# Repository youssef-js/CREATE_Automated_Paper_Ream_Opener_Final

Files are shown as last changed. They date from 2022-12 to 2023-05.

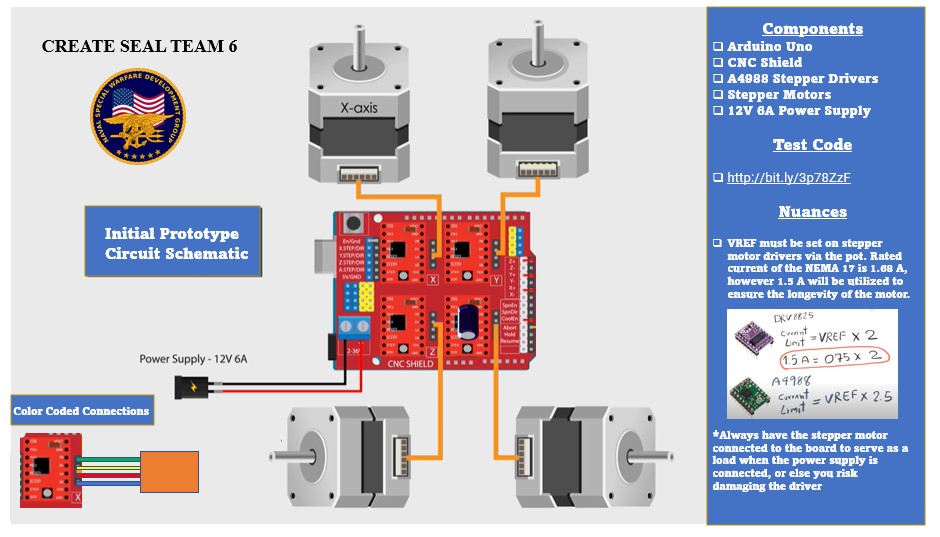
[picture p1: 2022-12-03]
Misc/CREATE_Circuit_Schematic.jpg

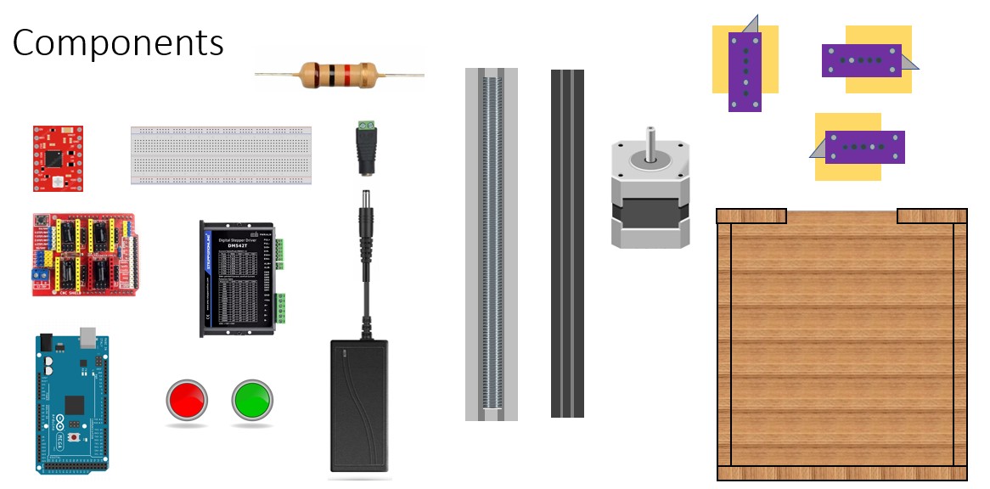
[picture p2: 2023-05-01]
Misc/CREATE_Final_Components.jpg

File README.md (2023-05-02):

# CREATE-Competition-Automated-Paper-Ream-Opener

 Fall 2022 - Spring 2023 
 ECE Design Lab
 
 The Center for Disability Services mailing center, which processes enormous amounts of mail per day
supporting official New York State mailing operations, has partnered with students to develop a system that assists
disabled workers. The center uses an estimated 50,000 – 100,000 pieces of paper per day. This paper is manually
opened from reams of paper containing 500 sheets each, therefore, approximately 100-200 reams of paper must be
opened per day. The center would like to hire people with disabilities to open the reams of paper, but this is difficult due
to physical dexterity issues and the large number of paper cuts the disabled workers often suffer when trying to do this
job. 

The goal of this project is to develop a system that automatically opens reams of paper in a safe and effective way.

 ### Repository Contents
 
 In the interest of transparency all project reports have been included. Reading through this documentation will provide an individual with information on key milestones that were achieved during the progressive evolution of the product. Specifically the "Reports" folder contains the following: 
 
 * Logical Design Report
 * Physical Design Report
 * Experimental Design Report 
 * CREATE_Experimental_Results_and_Discussion

 Furthermore, within the "Presentations" folder viewers have been provided with a final copy of the presentation slides for both the fall and spring semesters utilized within the classroom setting that exemplify the accomplished work within a condensed format.

 Lastly, in the scenario where an individual may wish to replicate the design we have provided the source code from the Fall and Spring semester that is used to control the logic behind the device. The initial circuit schematic, initial preliminary prototype model, final circuit schematic, final 3D model and lastly a compilation of the fianl components being used have also been included, these can be found within the "Misc" folder.
 
  ### System Parts
  
  The system was designed with the intention of being completely reproducible by any individual with the desire to do so. As such for the convenience of the prospective designer, the utilized components and their respective links are compiled below:
  
  1. Drive System Components

     * Belt Driven Nema 17: 500mm 1070-Bundle
  
       Link: https://openbuildspartstore.com/v-slot-nema-17-linear-actuator-bundle-belt-driven/
       
     * Belt Driven Nema 17: 500mm 1070-Bundle
  
       Link: https://openbuildspartstore.com/v-slot-nema-17-linear-actuator-bundle-belt-driven/
       
     * Belt Driven Nema 17: 250mm 1070-Bundle
  
       Link: https://openbuildspartstore.com/v-slot-nema-17-linear-actuator-bundle-belt-driven/
       
     * STEPPERONLINE NEMA 23 Stepper Motor 3.0A
  
       Link: https://www.amazon.com/gp/product/B077Z5QJCL/ref=ewc_pr_img_2?smid=AWQBCGWISS7BL&psc=1
       
     * NEMA23 Stepper Motor Mounting Plate
  
       Link: https://www.amazon.com/gp/product/B0836P59M4/ref=ppx_yo_dt_b_search_asin_title?ie=UTF8&psc=1
       
     * Saiper 5pcs GT2 20 Teeth 6.35mm Bore Timing Pulley
  
       Link: https://www.amazon.com/gp/product/B07MGMBX3N/ref=ewc_pr_img_3?smid=A3ILYKI8R26I7D&th=1
       
     * Threaded Rod with Cart and NEMA Stepper Motor Apparatus
  
       -Obtained from Public Laboratory Supplies, it had been fully assembled by another individual

  2. Control-Oriented Components
  
     * CNC Shield Expansion Board V3.0 + 4Pcs A4988 Stepper Motor Driver
  
       Link: https://www.amazon.com/Shield-Expansion-Stepper-Engraver-Printer/dp/B07DXNZ9PS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

     * 12V 6A Power Supply
  
       Link: https://www.amazon.com/Signcomplex-Supply-Transformer-Switching-Adapter/dp/B074HV582Q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

     * 24V 6A Power Supply
  
       Link: https://www.amazon.com/Adapter-100-240V-Transformers-Security-Computers/dp/B08Z7X9F1V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
       
     * Arduino Mega 
  
       Link: https://www.amazon.com/ELEGOO-ATmega2560-ATMEGA16U2-Projects-Compliant/dp/B01H4ZDYCE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
       
  3. Crucial Supplies
 
     * Wires
  
       Link: https://www.amazon.com/dp/B08B8XX89H/ref=twister_B09H6XQRJG?_encoding=UTF8&th=1
       
     * Bulk Pack of A4988 Stepper Motor Drivers
  
       Link: https://www.amazon.com/HiLetgo-Stepstick-Stepper-Printer-Compatible/dp/B07BND65C8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

     * DM542T STEPPERONLINE CNC Stepper Motor Driver
  
       Link: https://www.amazon.com/STEPPERONLINE-1-0-4-2A-20-50VDC-Micro-step-Resolutions/dp/B06Y5VPSFN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
       
     * DM542T STEPPERONLINE CNC Stepper Motor Driver
  
       Link: https://www.amazon.com/STEPPERONLINE-1-0-4-2A-20-50VDC-Micro-step-Resolutions/dp/B06Y5VPSFN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
       
     * 18mm Snap-off Blades by HEIKIO
  
       Link: https://www.amazon.com/Snap-Off-50-Pack-Quality-Stainless-Replacement/dp/B07XRTWWMS
       
     * LED Illuminated Push Buttons
  
       Link: https://www.amazon.com/gp/product/B01M7PNCO9/ref=ox_sc_act_title_1?smid=A3H7VB6FZ4M9FM&psc=1
       
     * 2pcs 2040 V Slot 600mm Aluminum Extrusion
  
       Link: https://www.amazon.com/dp/B0B9WY6PK9?ref=ppx_yo2ov_dt_b_product_details&th=1
       
     * 460PCS M4 Screws Metric Button Head
  
       Link: https://www.amazon.com/gp/product/B09YM7V1JC/ref=ppx_yo_dt_b_asin_title_o02_s00?ie=UTF8&th=1
       
     * Iverntech 20pcs Black Aluminum Corner Bracket
  
       Link: https://www.amazon.com/dp/B091GH5QKF?ref=ppx_pop_mob_ap_share&th=1

  4. Store-Bought Components
  
     * Wooden Planks
  
       Store: Home Depot
     
     * Acrylic Top Cover
  
       Store: Lowes

 ### Itemized Expenses
  
| Category | Item | Price |
| --- |:---:| -----:|
| Drive System |Belt Driven Nema 17: 500mm 1070-Bundle |$117.99|
| |Belt Driven Nema 17: 500mm 1070-Bundle |$117.99|
| |Belt Driven Nema 17: 250mm 1070-Bundle |$111.99|
| |STEPPERONLINE NEMA 23 Stepper Motor 3.0A |$31.98 |
| |NEMA23 Stepper Motor Mounting Plate |$9.49  |
| |Saiper 5pcs GT2 20 Teeth 6.35mm Bore Timing Pulley |$8.39  |
| |Threaded Rod with Cart and NEMA Stepper Motor Apparatus |FREE |
| | | |
| Control-Oriented Components|CNC Shield Expansion Board V3.0 + 4Pcs A4988 Stepper Motor Driver  |$15.39 |
| |12V 6A Power Supply |$19.99 |
| |24V 6A Power Supply |$15.98 |
| |Arduino Mega |$20.99 |
| | | |
| Crucial Supplies | Wires |$14.94 |
| |Bulk Pack of A4988 Stepper Motor Drivers |$9.89  |
| |DM542T STEPPERONLINE CNC Stepper Motor Driver |$28.99 |
| |DM542T STEPPERONLINE CNC Stepper Motor Driver |$28.99 |
| |18mm Snap-off Blades by HEIKIO |$21.99 |
| |LED Illuminated Push Buttons |$18.86 |
| |2pcs 2040 V Slot 600mm Aluminum Extrusion |$86.97 |
| |460PCS M4 Screws Metric Button Head |$17.99 |
| |Iverntech 20pcs Black Aluminum Corner Bracket |$18.99 |
| | | |
|Store-Bought |Wooden Planks |Stakeholder Expense|
| |Acrylic Top Cover |Stakeholder Expense| 
| | | |
|Grand Total |-------------  |$717.79|

   ### Software Dependencies
   
   In the context of software dependencies there is none for the traditional user. This apparatus requires no external downloads and is advertised as a complete stand-alone product.
   
However, when initially setting up the device one must upload the source code onto the microcontroller. The first step is to download the Arduino IDE, the appropriate link is found below:

Link: https://www.arduino.cc/en/software

At this stage the setup in terms of software has been completed. Please download the source code provided within this repository and upload to the microcontroller to begin using the apparatus.

### Replication

In the interest of successfully replicating the aforementioned progress a concise check list has been provided below.

 1. Watch the instructional videos provided below:
  
     Basics
     * Link: https://www.screencast.com/t/LzzzPJ7e0wt

     Assembly of Linear Rail Kits
     * Link: https://www.youtube.com/watch?v=tHn-gffborc&ab_channel=OpenBuilds

     Specifics of Analog Blade Holders
     * Link: https://youtu.be/Tv00ml124e8

     NYSID CREATE Final Video Submission
     * Link: https://www.youtube.com/watch?v=cMDn14l95jw&ab_channel=MazinChater
       
Now that sufficient context has been provided an individual would proceed by purchasing the displayed equipment articulated within the video format. A complete list of parts with purchasing links has been organized up above in the "System Parts" section.
    
  2. Purchase Relevant Equipment
  
Lastly, the final step of the procedure is to recreate the circuit connections displayed within the "Misc" folder of this repository. After this has been accomplished an indvidual may upload the source code to the microcontroller.
    
  3. Follow Circuit Schematic and Upload Source Code
 
It will be known whether or not successful replication has been achieved based on the performance of the apparatus in comparison to the ideal case displayed in the instructional video.

### NYSID CREATE Competition



1st place finish at the NYSID CREATE competition. 
Beyond the prize money, the work is having a real impact.  It has enabled the Center for Disability Services Mailing Center to hire additional workers with disabilities.
### Personnel and Funding

This project is completely sponsored by New York State Industries for the Disabled (NYSID) and allows the respective designers to take part in the CREATE (Cultivating Resources for Employment with Assistive TEchnology) competition.

Designers

1. Youssef Jalwaj Soubai

2. Mazin Chater

3. Abdullah Qureshi

Faculty Mentors/Support

1. Jonathan Muckell

2. Mike Denmark

Special thanks to Alex Demitraszek, customer care manager of the Center for Disability Services.

Developed in ECE490: Design Lab; in the Electrical & Computer Engineering Department.

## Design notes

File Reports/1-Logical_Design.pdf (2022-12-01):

PP-2017 V2.1

ANALYSIS & LOGICAL DESIGN | 1

# CREATE Competition: Automated Ream Opener (Analysis & Logical Design)

Abdullah Qureshi, Youssef Jalwaj-Soubai, Mazin Chater

Activity Report

Abstract—The Center for Disability Services mailing center, which processes enormous amounts of mail per day supporting official New York State mailing operations, has partnered with students to develop a system that assists disabled workers. The center uses an estimated 50,000 – 100,000 pieces of paper per day. This paper is manually opened from reams of paper containing 500 sheets each, therefore, approximately 100-200 reams of paper must be opened per day. The center would like to hire people with disabilities to open the reams of paper, but this is difficult due to physical dexterity issues and the large number of paper cuts the disabled workers often suffer when trying to do this job. The goal of this project is to develop a system that automatically opens reams of paper in a safe and effective way.

Index Terms—Arduino, NEMA, automated ream opener

✦

### 1 THE PROBLEM

MAILING centers typically require large quantities of paper to meet their daily demands. As such, reams of paper must be opened safely and efficiently in a proportionally high demand. The Center for Disability Services would like to develop a system which meets these requirements particularly as a tool to assist disabled workers. A viable solution would decrease time to open each ream while simultaneously being safe and accessible to disabled workers. Ideally, it would also allow the Center for Disability Services to hire additional disabled individuals specifically to operate the final system.

### 2 INSPIRATION

When doing background research on the topic, there was no automated system that opened

- Mazin Chater ,
E-mail: mchater3@albany.edu
- Youssef Jalwaj-Soubai ,
E-mail: yjalwaj-soubai@albany.edu
- Abdullah Qureshi ,
E-mail: aqureshi@albany.edu
Electrical and Computer Engineering Department University at Albany

a ream of paper. There were implementations that operated on paper, however. Of these, most relevant was an automated letter opener and an Arduino based paper cutter. When considering the former, it was worth noting how the letters were opened precisely without damaging the inside contents. This is a similar amount of space between the outside sheet and interior paper of a ream, leading to the conclusion that a blade of high precision could open the outside sheet without cutting any interior papers. Of the latter, the Arduino based paper cutter used a NEMA stepper motor to move a blade left and right perpendicular through a sheet of paper, thereby making equal cuts of length specified by the user. This design led to an epiphany regarding the use of a stepper motor to cut across potentially each of the four sides of the ream to separate the outside layer.

### 3 DESIGN CONSTRAINTS

There are limitations placed on a potential implementation. Most evidently, testing will be a primary focus and is somewhat limited due to the lack of readily available access to reams of paper. Additionally, funds are limited and restrain the amount of trial-and-error in terms

Activity Report

2 | ANALYSIS & LOGICAL DESIGN

of system designing. Finally, there is a deadline
of completion by April 2023.
- Testing: Although available in high capacity at the Center for Disability Services mailing center, it is limiting to consider scheduling, travel, etc to perform frequent tests.
- Cost: The Center for Disability Services has allocated a balance of one thousand dollars to build the desired system.
- Time: The design should be complete and in use well before the start of the CREATE design competition in April.

### 4 PROPOSED SOLUTION

The proposed device is a preliminary prototype that reflects the designers aptitude towards testing. Focusing on this notion the following engineering diagram has been developed. An individual should take head that the inspiration from the letter opener is the driving concept for this implementation.

### 4.1 Engineering Diagram

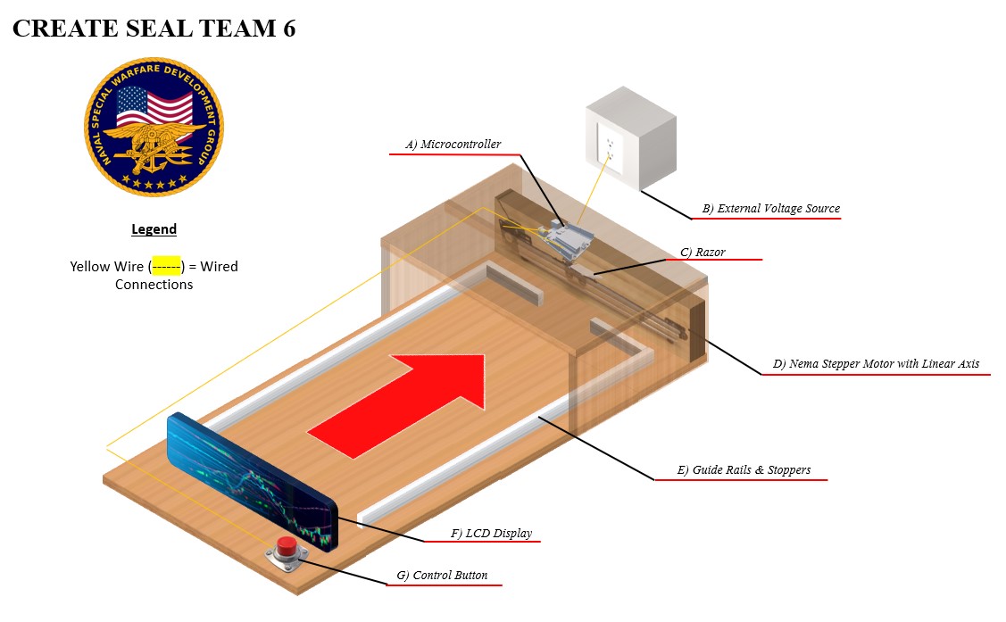
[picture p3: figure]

Figure 1. Annotated diagram of the proposed solution.

Physically speaking the device is quite simple in nature and requires minimal overhead to implement. The design is centered around a linear axis rail operated by a NEMA stepper motor. This contraption is capable of controlled uniform movement and as such when a razor blade is attached to the sliding linear cart it will ideally make clean lacerations to the paper ream cover. A user interacts with the system via a button press that controls the operation of the linear rail. Along the base of the apparatus there are guiding protuberances that orient the ream in the most optimal setting. These ”stoppers” ensure that only the cover of the ream will be slit, thereby leaving the contents unperturbed.

### 4.2 System Requirements

4.2.1 System User
The user that will interact with the system is an employee from the Center for Disability Services mailing center. All that will be asked of this individual is the ability to lift and push a ream of paper into its proper setting as well as the ability to push a button. If both of these qualities are satisfied one will have no issue operating the proposed solution.

4.2.2 Functional Requirements
Following are the most important functional requirements.
1) Paper Ream Cutting Ability: The system should have the ability to slit the desired ends of the paper ream in order to make the paper ream opening easy.
2) Safety: Since the users of the system are physically disabled, its a mandatory requirement of the system to be completely safe to use.
3) Ease of Use: Since the users of the system are physically disabled, its a mandatory requirement of the system to be very easy to use.

4.2.3 Non-Functional Requirements Following are the most important non-functional requirements of the system.
1) Capacity: The system should have the ability to open 200 reams of paper a day.
2) Ability to work with different ream size: It is a desired quality of the system to be able to work with different size of paper reams.
3) Complete Package Opening: Ideally the system should be able to completely open the paper ream although cutting the ends of the paper ream is sufficient.

PP-2017 V2.1

SURNAME et al. | 3

### 4.3 Justification

The belt driven actuator design was chosen
mainly because of its ease of use and paper ream opening ability. The current design is easier to use than the moving arm package opener because it is more compact and will potentially contain a single button to control the blade. The idea of a moving arm package opener design was built around two arms that go into the flaps of the paper ream and then move along the y axis to tear the paper ream. The moving arm package opener design was safer to use because it did not contain the a cutting blade but it would not be easy to use and would be very less compact. Based on these results our team decided to go with the belt driven actuator design.

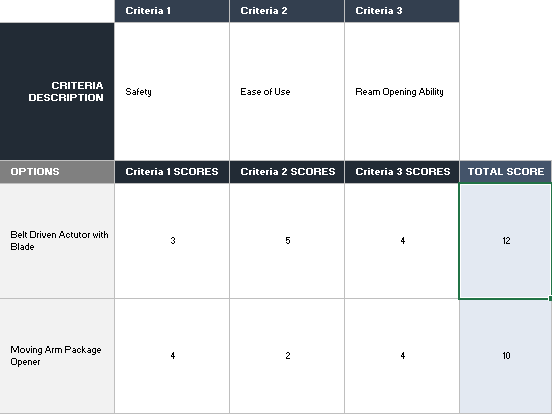
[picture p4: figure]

Figure 2. Decision Matrix

### 4.4 Ethical Concerns

One of the most important ethical concerns that our design addresses is user safety. Since our design contains a blade that moves along the x axis to open the ream of paper, the danger of a user getting a cut increases dramatically. In order to mitigate potential harm caused by the system the belt driven actuator with blade will be put into a wooden box such that the only thing that can be put in to the box is just the ream of paper. Moreover, the stepper motors that control the motion will be controlled by a button. This will ensure that the stepper motors does not cause the blade to move without user input.

### 5 INITIAL PROTOTYPE

Our initial prototype consists of a wooden box with a belt driven actuator to which a blade is attached. The belt driven actuator allows the blade to move along the x axis. The belt driven actuator is controlled by a stepper motor, which allows movement in the positive and negative x axis. In order to ensure the safety of the user, the control of the stepper motor will be done by a button outside the wooden casing. The user will place the paper ream inside the apparatus, the stoppers will restrict the user from pushing the paper ream too close to the blade. After placing the paper ream , the user will push the button for the actuator to start and the blades will make a cut to the specific side of the paper ream. The user can switch the side of the paper ream to apply cuts on different sides of the paper ream to make the package easier to open. After applying the cuts the user can take the paper ream and dump the contents. One prospective engineering problem that might cause delays is finding the optimal distance for which to stop the paper ream, such that the blade does not cause damage to the paper inside the ream. One solution to the problem is experimenting with the reams and through trial and error finding the specific distance that will allow for the package to be cut without harming the paper inside.

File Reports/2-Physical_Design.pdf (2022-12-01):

PP-2017 V2.1

PHYSICAL DESIGN | 1

# Automated Ream Opener

# (Physical Design)

Mazin Chater, Abdullah Qureshi, Youssef Jalwaj-Soubai

Activity Report

✦

### 1 PHYSICAL DESIGN

### 1.1 Engineering Diagram


Figure 1. Annotated diagram of the proposed solution.

Physically speaking the device is quite simple in nature and requires minimal overhead to implement. The design is centered around a linear axis rail operated by a NEMA stepper motor. This contraption is capable of controlled uniform movement and as such when a razor blade is attached to the sliding linear cart it will ideally make clean lacerations to the paper ream cover. A user interacts with the system via a button press that controls the operation

- Mazin Chater,
E-mail: mchater3@albany.edu,
- Youssef Jalwaj-Soubai,
E-mail: yjalwaj-soubai@albany.edu,
- Abdullah Qureshi,
E-mail: aqureshi@albany.edu, University at Albany.

of the linear rail. Along the base of the apparatus there are guiding protuberances that orient the ream in the most optimal setting. These ”stoppers” ensure that only the cover of the ream will be slit, thereby leaving the contents unperturbed.

### 1.2 Parts List & Budget

The noted parts are preliminary and likely subject to change. Likewise, cost is expected to increase as additional components may be necessary. Observe the parts list and budget shown on Table 1. These detail the components germane to our prototype.

### 1.3 Software Dependencies

The following represents the software dependencies of the system.
1) Software: Arduino IDE
The open-source Arduino Software (IDE) is used to write the code and upload it to the board. The code controls the rotation speed, and time the stepper motor rotates for. The code also contains the logic through which the stepper motor rotates in one direction when the push button is pressed and then the opposite direction when the push button is pressed again.

### 1.4 Equipment Dependencies

The following represents the equipment needed for testing the system.
1) Equipment: Paper Ream

Activity Report

2 | PHYSICAL DESIGN
Item | Part # | Supplier | Cost | Description
Belt Driven NEMA 17 | 1070-Bundle | OpenBuilds | $94 | Drive system
Wires | 20 AWG | Amazon | $15 | Connections
Motor Driver | A4988 | Amazon | $10 | Integrates NEMA 17 and microcontroller
Microcontoller | Ard. MEGA R3 | Amazon | $21 | Executes Software Logic / Controller
Razor Blades | SK2H | Amazon | $5 | Cut ream
Paper Tray | CC431-60119ADF | Amazon | $20 | Load paper
Power Supply | 12V 2A | Amazon | $9 | Power NEMA
TOTAL | | | $175
Table 1
System Parts List & Budget

The purpose of the system is to remove the outer package of the paper ream.
2) Equipment: Belt Driven Linear Actuator This is an essential element of the system. A belt driven linear actuator is controlled by a stepper motor and contains a shuttle to which razor blades are attached. It enables the razor blades to move across the sides of the paper ream.
3) Equipment: Razor Blades
Utility knife blades are attached to the shuttle on the belt driven linear actuator. These blades enable the system to cut open the outer package of the paper ream.
4) Equipment: NEMA 17 Stepper Motor The stepper motor controls the belt driven linear actuator and is a key component in the functioning of the system. It is a necessary aspect in component testing.

### 1.5 System Integration & Standards

Engineering standards establish technical criteria, methods, processes and practices. In the current system, there is one communication standard (protocol) being utilized.
1) Standard: UART Protocol
UART ports communicate between only two devices (transmit and receive). Both devices must agree on data and communication speed ahead of time and requires complex hardware. There is no control over when the data is sent and no guarantee that both sides are running at the same rate. To achieve reduced data rates, at least one start and stop bit is a part of each frame of data.

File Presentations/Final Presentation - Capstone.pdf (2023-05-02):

# Automated

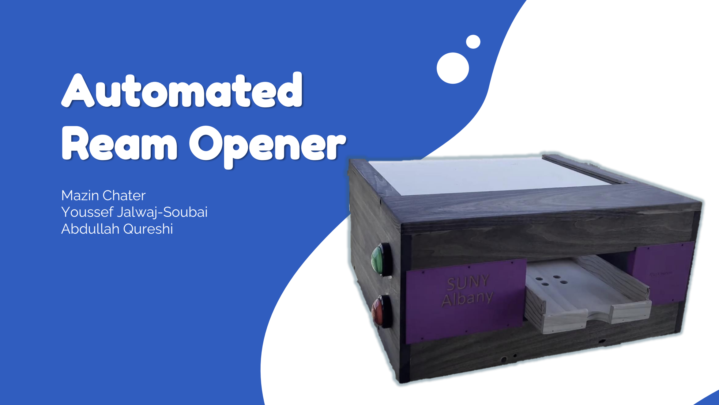
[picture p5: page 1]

# Ream Opener

Mazin Chater
Youssef Jalwaj-Soubai
Abdullah Qureshi

# Overview

Previous limitations

## The Issue

How requirements
influenced the design

## Requirements

Core functionality & how
our design addresses the
issue

## Solution

A closer look at key
components & code
functionality

## Features

How our solution will be
used

## Impact

Slideshow & Q/A

## Wrap Up

01

04

02

05

03

06

# Problem

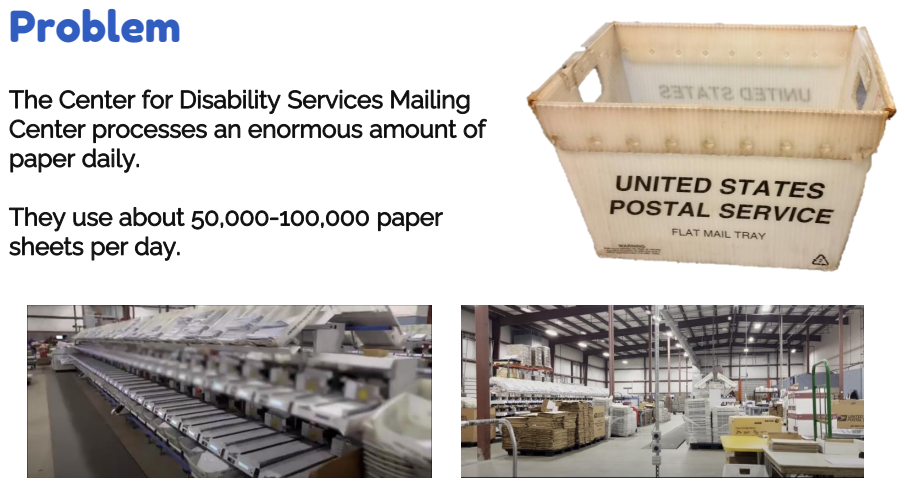
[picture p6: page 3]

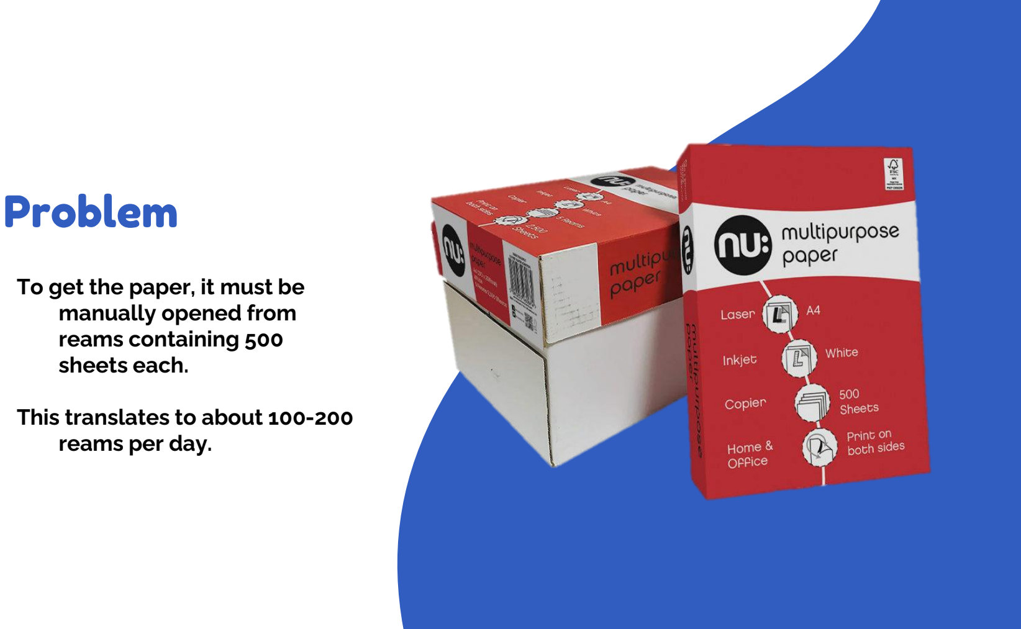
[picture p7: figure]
Problem; To get the paper, it must be manually opened from reams containing 500 sheets each.; This translates to about 100-200 reams per day.

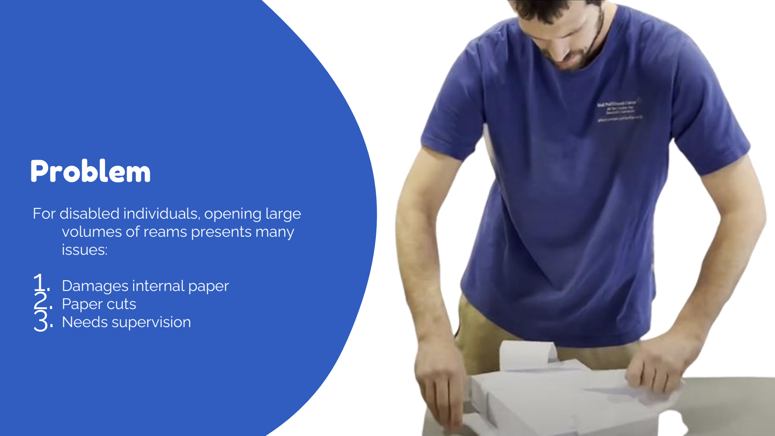
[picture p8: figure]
Problem; For disabled individuals, opening large volumes of reams presents many issues: 1. Damages internal paper 2. Paper cuts 3. Needs supervision

# System Requirements

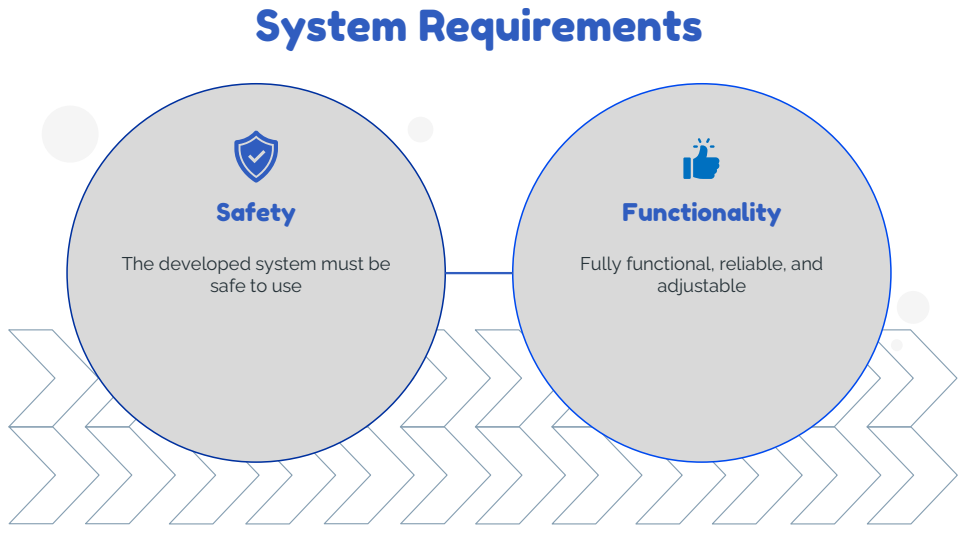
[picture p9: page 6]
Safety; adjustable; Functionality

The developed system must be

Fully functional, reliable, and

safe to use

# System Requirements

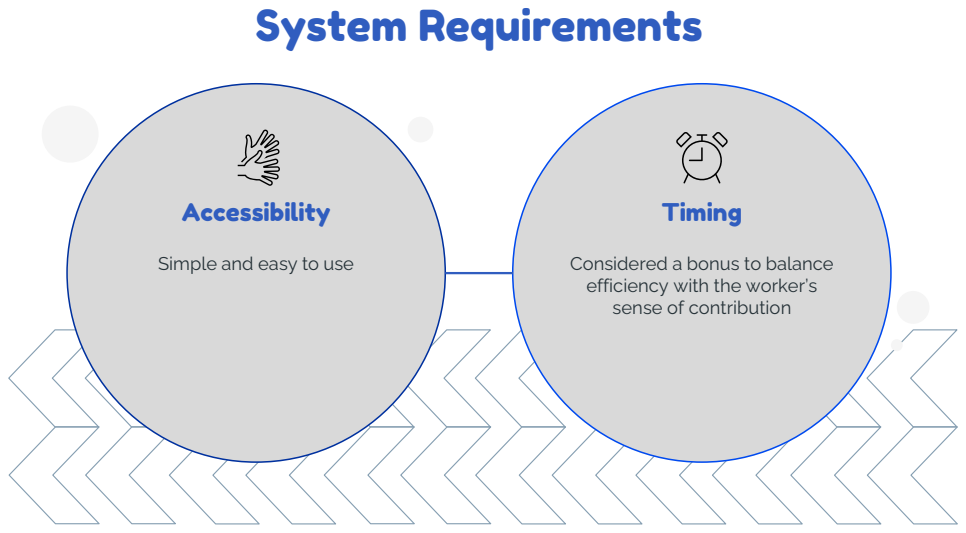
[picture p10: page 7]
Accessibility; Timing

Simple and easy to use

Considered a bonus to balance
efficiency with the worker’s
sense of contribution

# Function

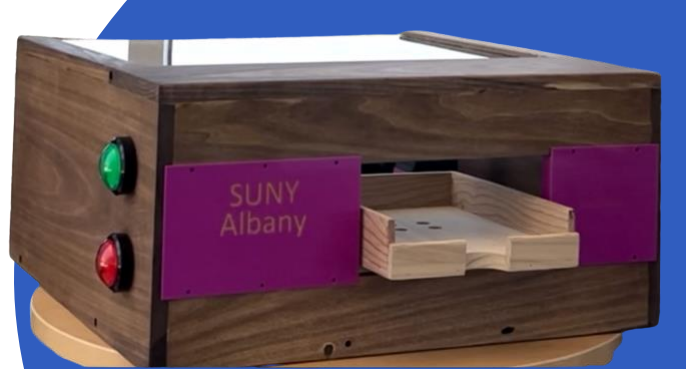
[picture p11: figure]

## 3) Blades Slice Outside Layer

## 4) Unsealed Ream Returns

## 2) Green Button Initiates Operation

## 1) Insert Wrapped Ream Into Tray

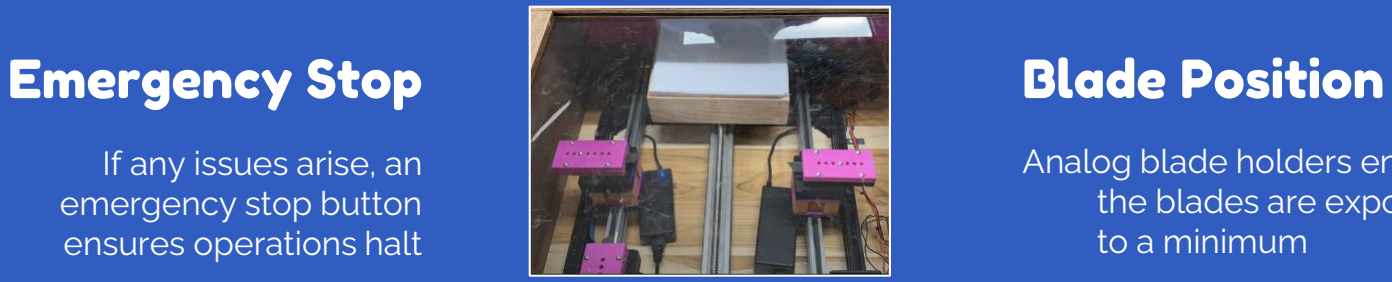
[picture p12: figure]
Emergency Stop; Blade Position

The carts are set in the back of the machine and only
move towards the ream
upon the start sequence

Analog blade holders ensure the blades are exposed
to a minimum

If any issues arise, an
emergency stop button
ensures operations halt

## Cart Position

The buttons are on the side of the machine to prevent
any accidental presses

## Button Position

# Safety Features

# Key Improvements

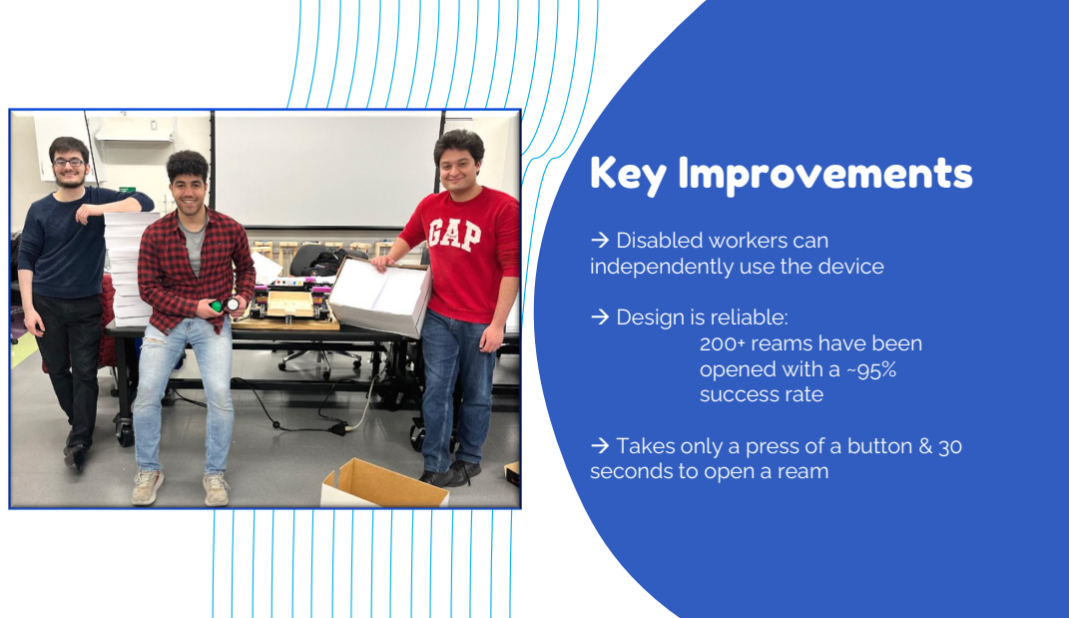
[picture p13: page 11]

→ Disabled workers can
independently use the device

→ Design is reliable:

200+ reams have been
opened with a ~95%
success rate

→ Takes only a press of a button & 30
seconds to open a ream

# Key Components

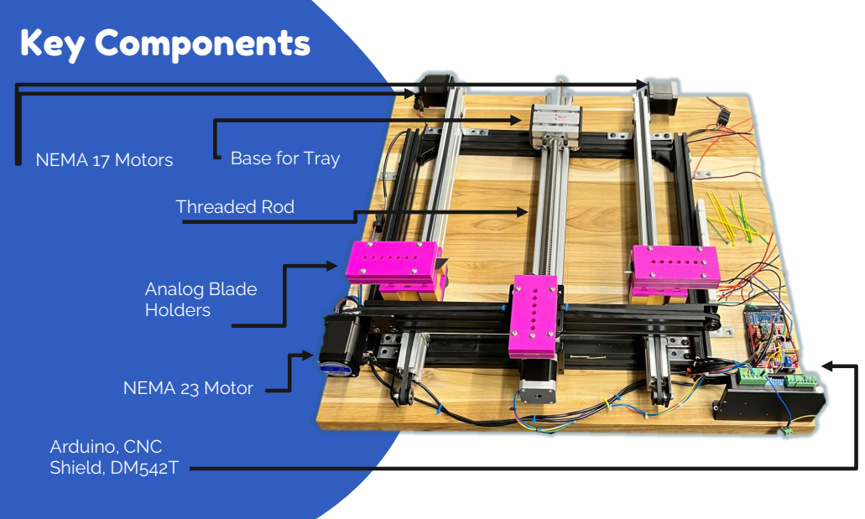
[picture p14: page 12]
NEMA 23 Motor; Analog Blade Holders; Threaded Rod; NEMA 17 Motors; Base for Tray; Arduino, CNC Shield, DM542T

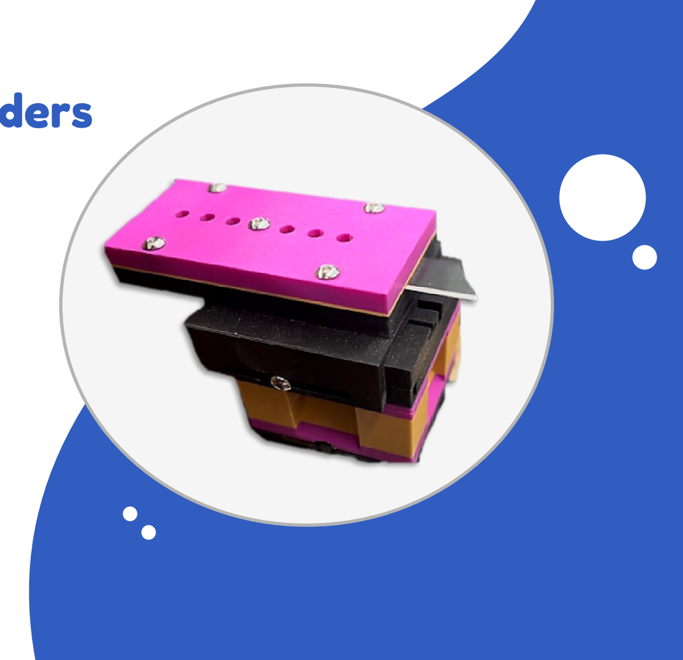
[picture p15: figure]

# Analog Blade Holders

→ Allows blades to be just barely
exposed

→ Blades are easily
interchangeable

→ Blades can be adjusted to hit the outside layer of paper without damaging inner contents

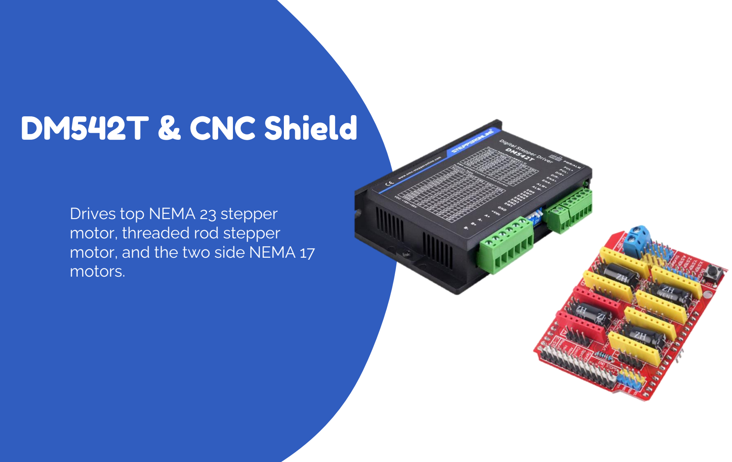
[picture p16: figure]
DM542T & CNC Shield; Drives top NEMA 23 stepper motor, threaded rod stepper motor, and the two side NEMA 17 motors.

# Circuitry

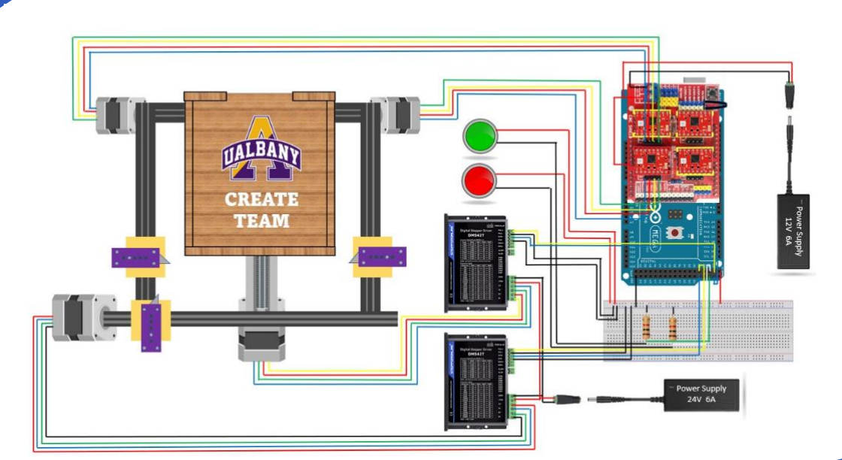
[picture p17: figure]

# Code

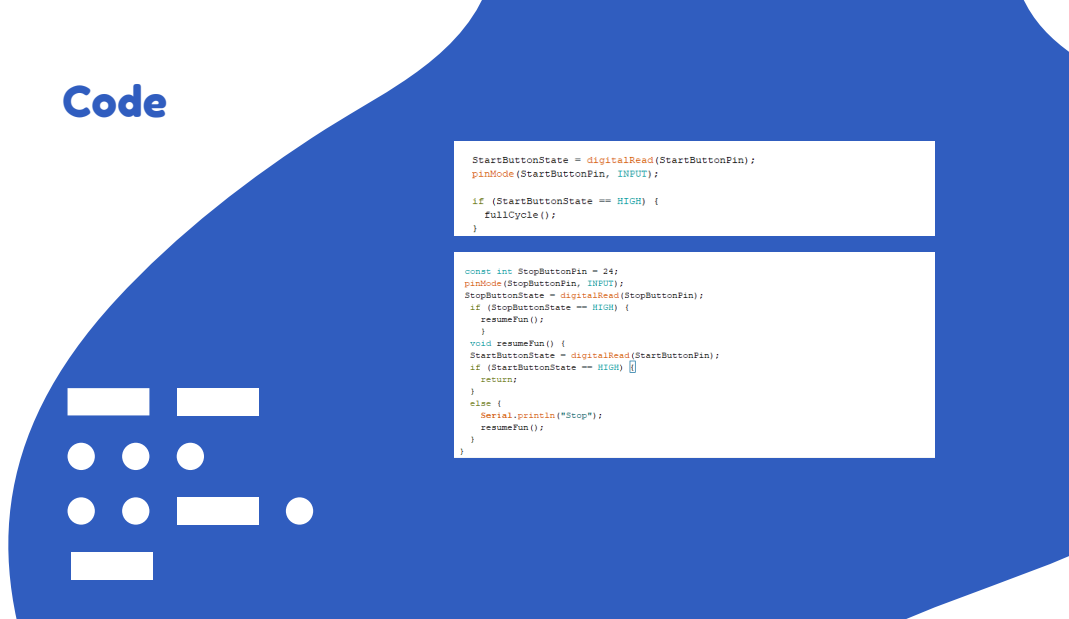
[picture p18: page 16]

# Code

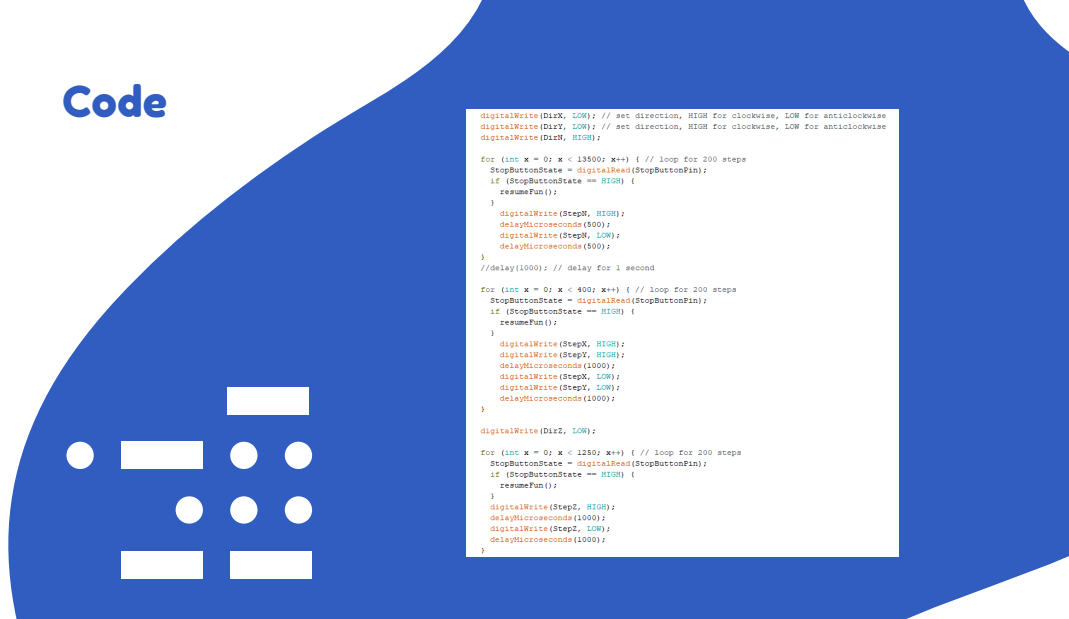
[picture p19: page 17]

# Code

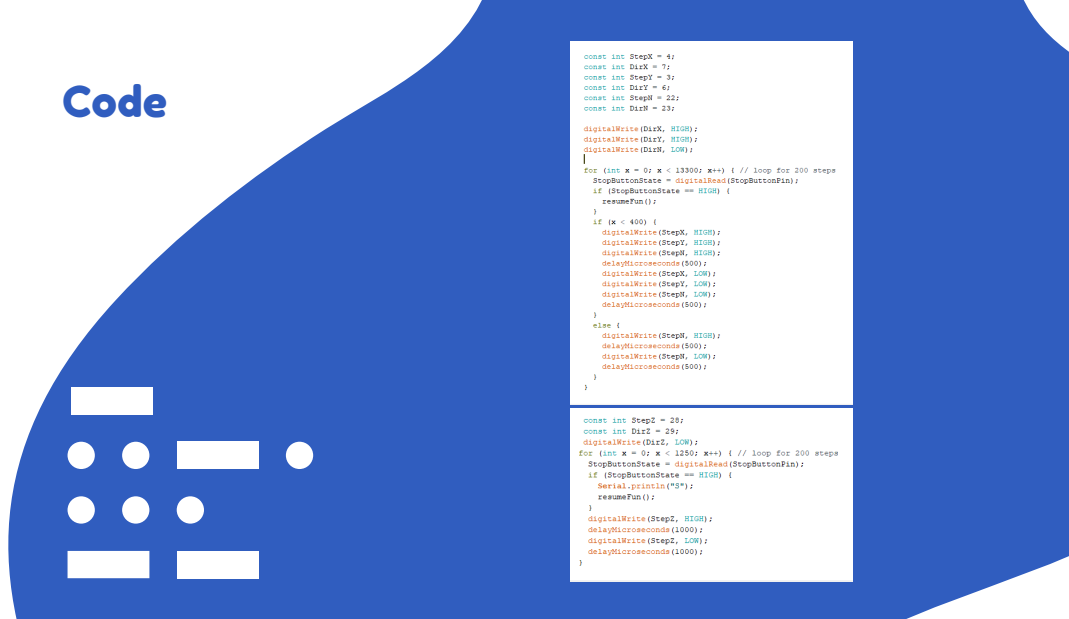
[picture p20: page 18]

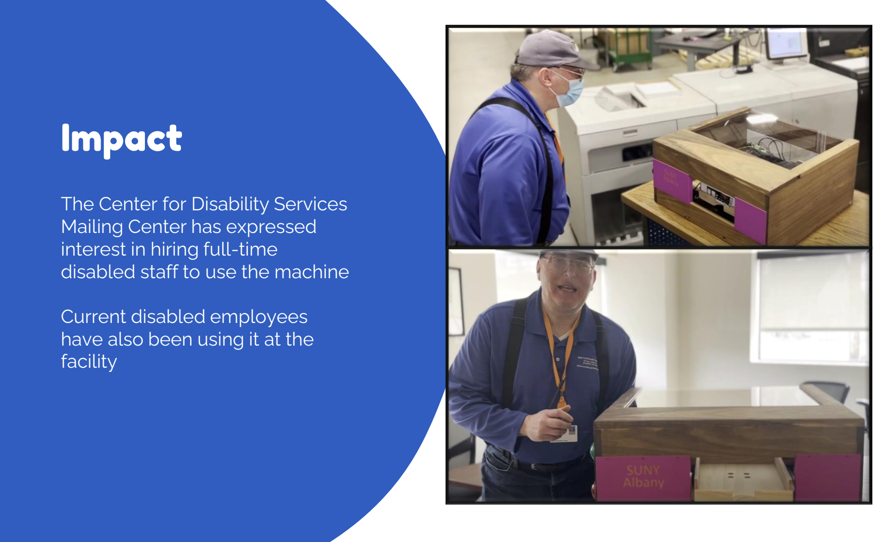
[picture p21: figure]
Impact; The Center for Disability Services Mailing Center has expressed interest in hiring full-time disabled staff to use the machine; Current disabled employees have also been using it at the facility

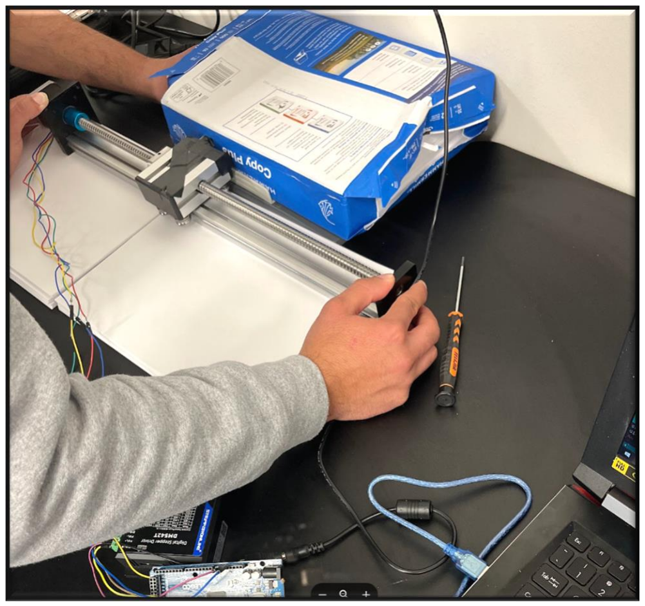
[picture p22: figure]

# September

# October

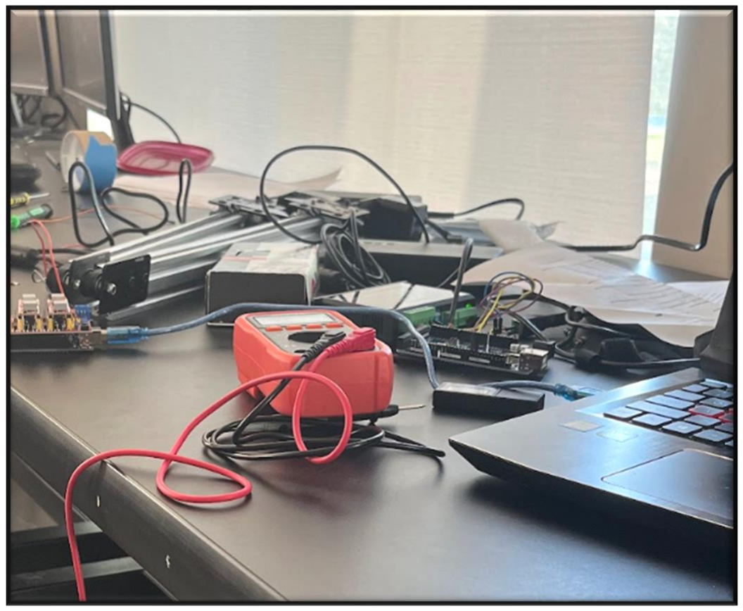
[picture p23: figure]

# November

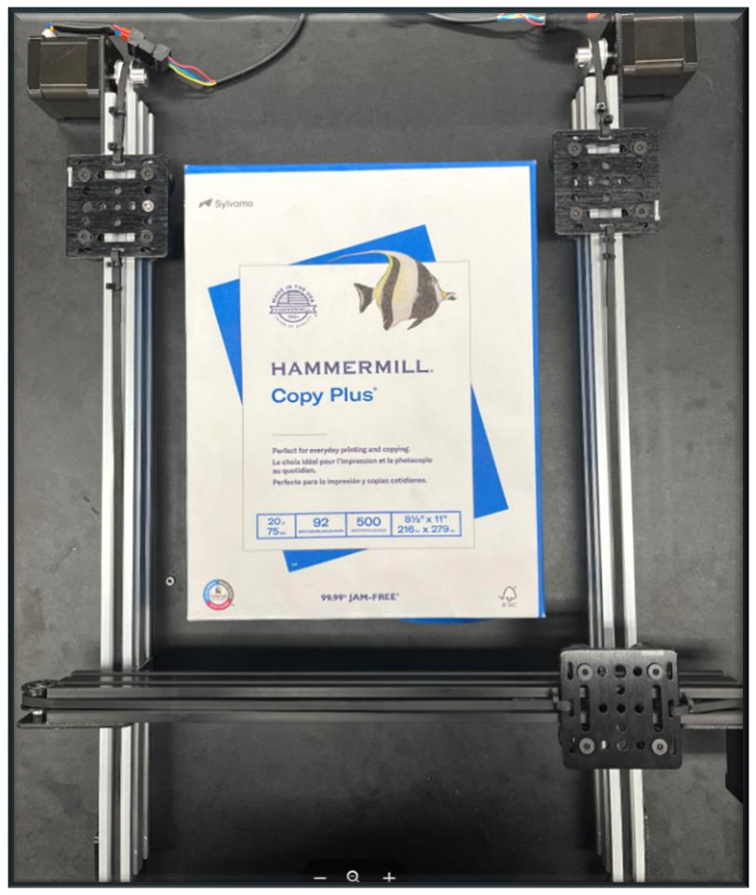
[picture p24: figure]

# December

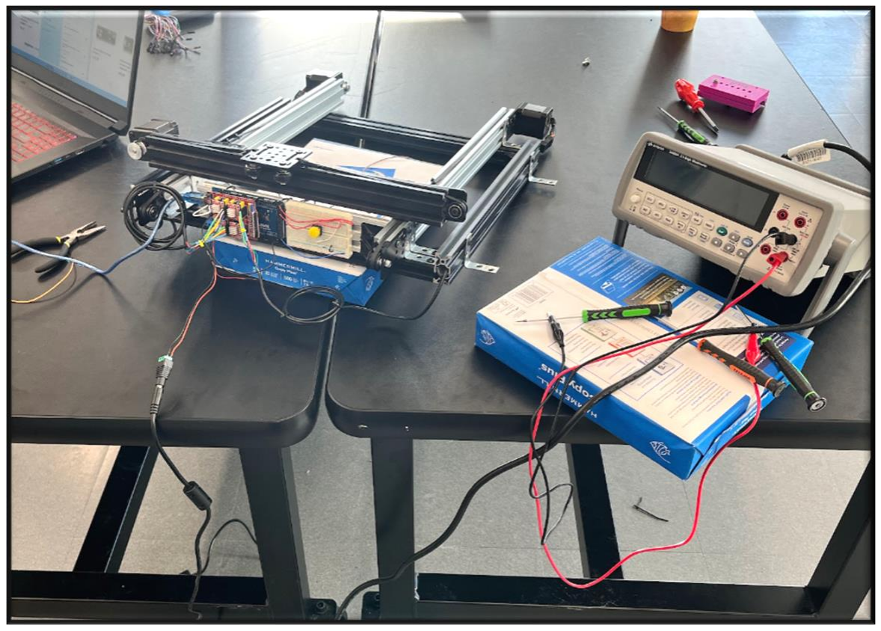
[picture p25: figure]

# January

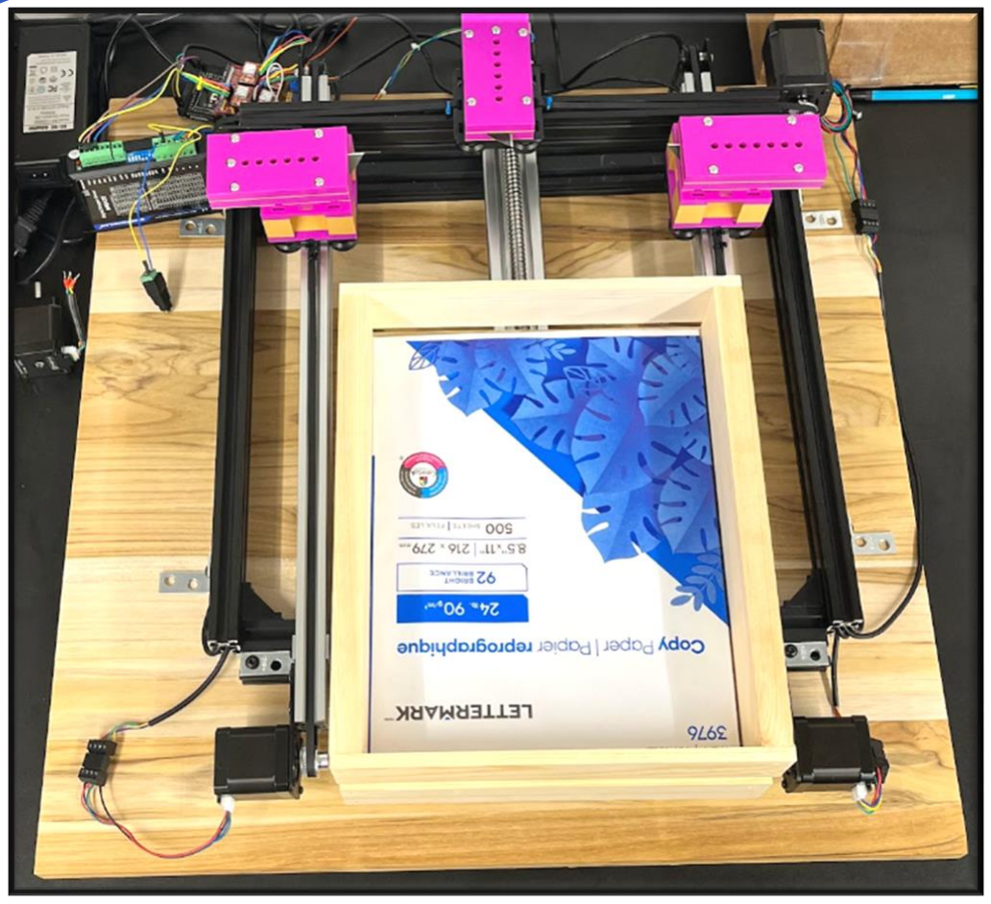
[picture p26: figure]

# February

# March


# April

# Thank you


Any questions?

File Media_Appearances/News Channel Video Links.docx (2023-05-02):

https://wnyt.com/stem-13/ualbany-students-prepare-for-competition-to-help-people-with-disabilities/


https://spotlightnews.com/news/2023/04/19/inclusive-innovations-break-down-barriers/


https://wnyt.com/top-stories/ualbany-students-win-big-in-science-symposium/


https://www.albany.edu/news-center/news/2023-engineering-students-earn-top-prize-create-symposium


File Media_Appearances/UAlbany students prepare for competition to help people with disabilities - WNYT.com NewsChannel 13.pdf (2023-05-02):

### 1 School Closings:

Click for full list of closings (https://wnyt.com/closings/)

Watch Live: (https://wnyt.com/live)

×
NewsChannel 13 Live at Noon (https://wnyt.com/live)

Learn more; Lifelock; Identity theft protection

# UAlbany students prepare for competition to help people with disabilities

By WNYT
April 15, 2023 - 1:02 PM

succeed at their jobs. EMAIL NEWSLETTERS; Email Address; Include Breaking News Alerts; SIGN ME UP »

College students will be competing to see which team developed the best technology to help people with disabilities

The competition is happening Monday, April 24 and will bring together five colleges presenting 10 inventions. UAlbany will be among the colleges participating.

This is the 9 annual competition.

The winners will receive $15,000 to be split between students, their universities, and rehabilitation organization partners.

For Related Stories: | UAlbany (https://wnyt.com/tag/ualbany/) | STEM (https://wnyt.com/tag/stem/)

th

### RECOMMENDED FOR YOU

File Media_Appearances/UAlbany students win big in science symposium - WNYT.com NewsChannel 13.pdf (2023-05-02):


# UAlbany students win big in science symposium

By WNYT
April 24, 2023 - 8:13 PM


Congratulations to students at the University at Albany for their first-place design in the 2023 CREATE symposium.

The competition was between college engineering students throughout the state who teamed up with organizations that are members of the New York State Industries for the Disabled.

The two parties partnered together to create inventions that assisted people with disabilities.

The inventions were judged by community business leaders who evaluated and scored the projects.

There were 10 inventions this year from five colleges and six organizations. This was their ninth annual competition.

UAlbany students partnered with the Center for Disability Services to create an automated paper ream opener. They will receive $15,000 in prize money.

### RECOMMENDED FOR YOU

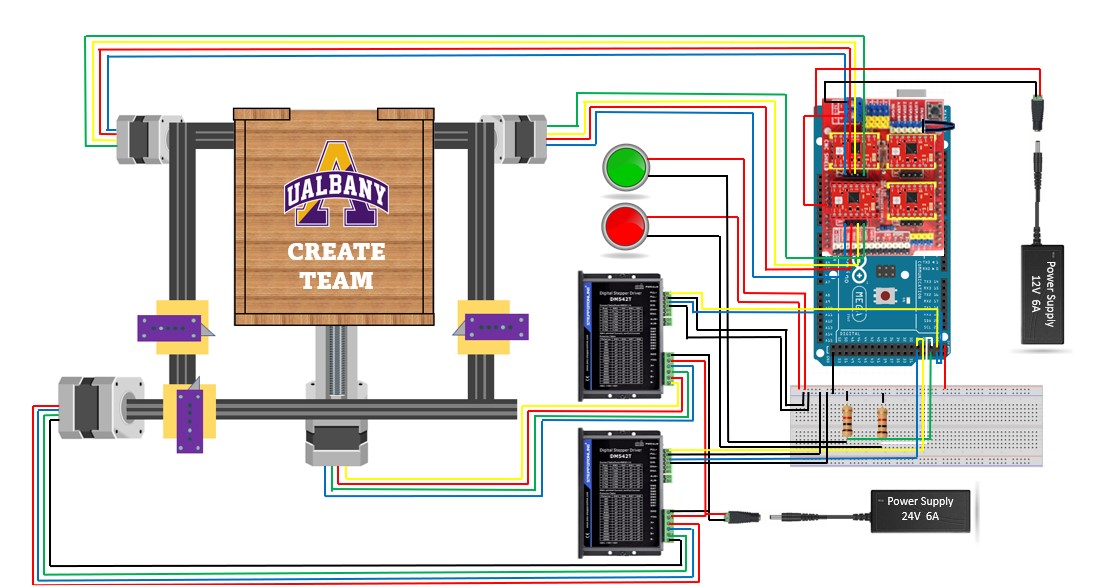
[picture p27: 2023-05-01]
Misc/CREATE_Final_Schematic.jpg

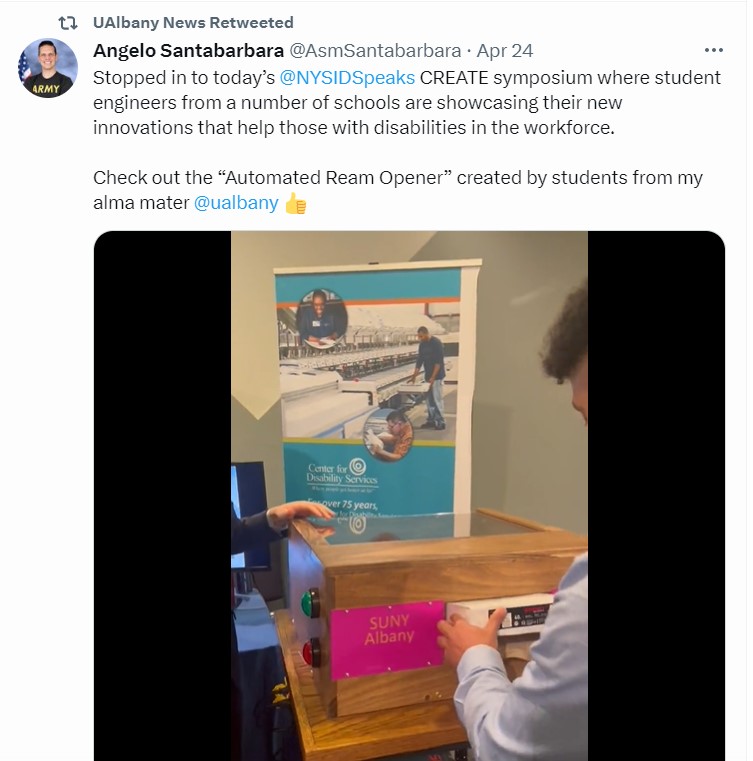
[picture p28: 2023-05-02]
Media_Appearances/Angelo_Santabarbara_Social_Media_Post.jpg

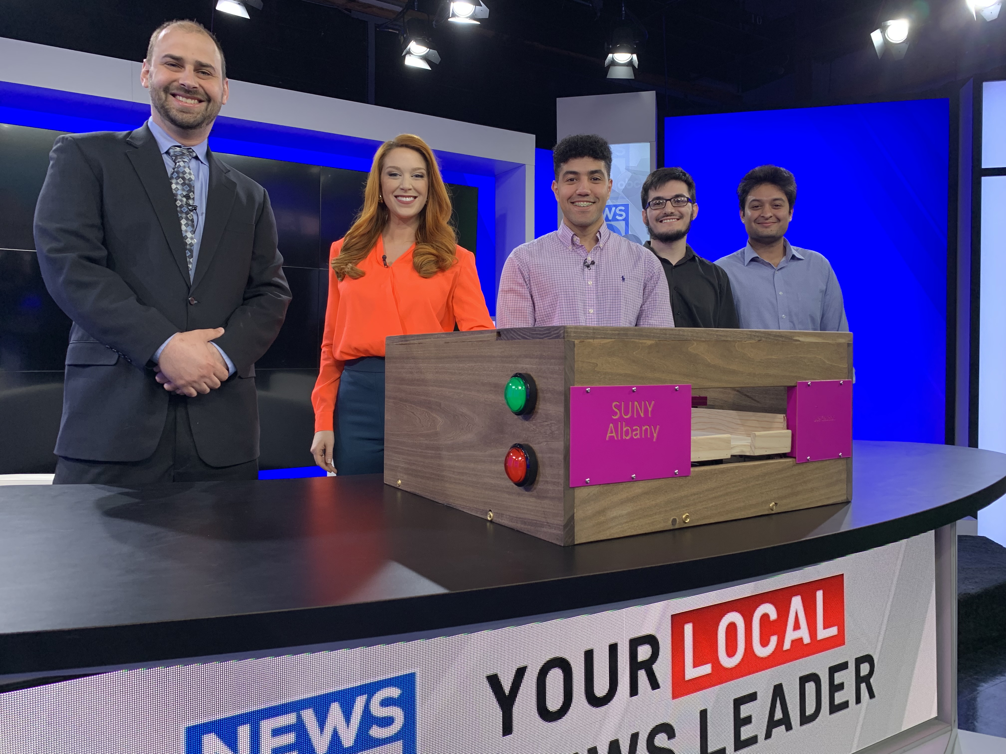
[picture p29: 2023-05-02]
Media_Appearances/News10_CREATE.jpg

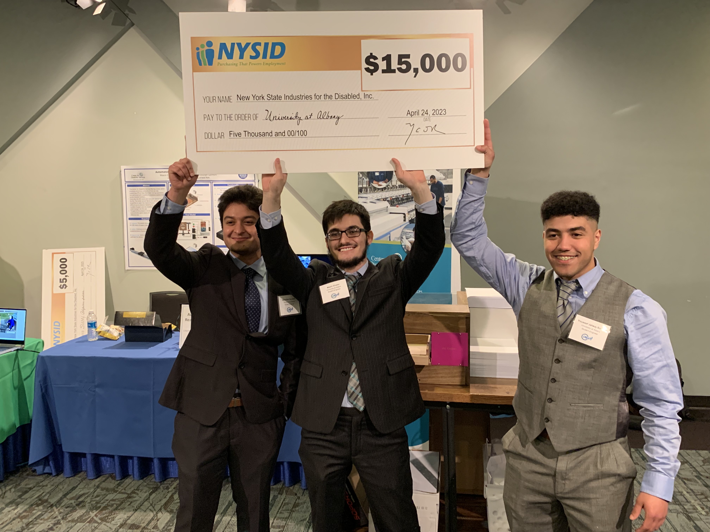
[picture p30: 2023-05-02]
Media_Appearances/CREATE_2023_1st_Place.jpg

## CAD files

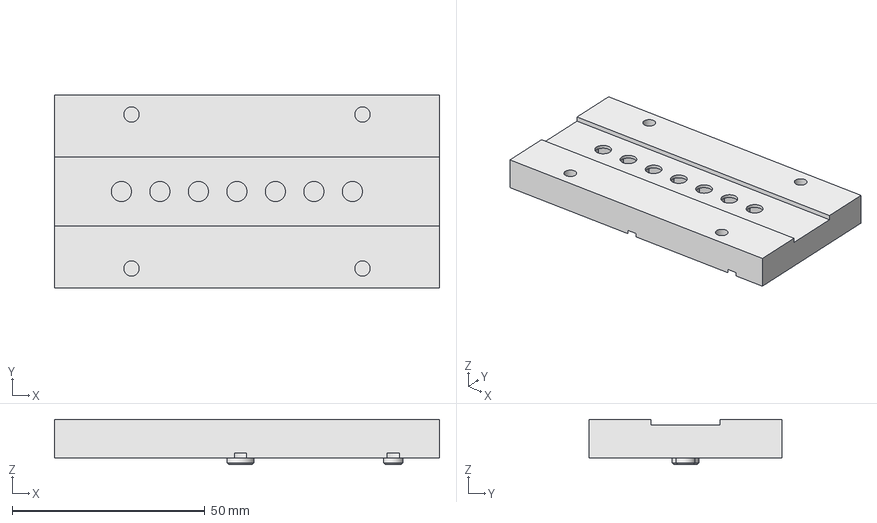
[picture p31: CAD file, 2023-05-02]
Misc/3D_Printed Components/BladeholderRevB.FCStd
100.0 x 50.0 x 11.8 mm

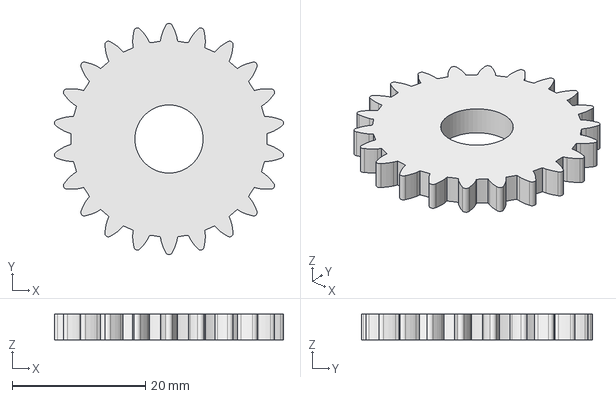
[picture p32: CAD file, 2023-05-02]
Misc/3D_Printed Components/SprocketRevC.FCStd
34.4 x 34.8 x 3.90 mm

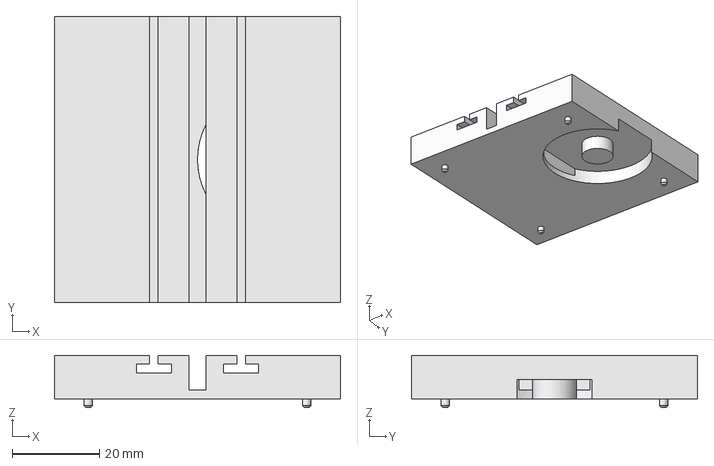
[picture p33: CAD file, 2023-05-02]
Misc/3D_Printed Components/Middle10mmAnalogueAdjSprocketHolder.RevC.FCStd
65.5 x 65.5 x 12.0 mm

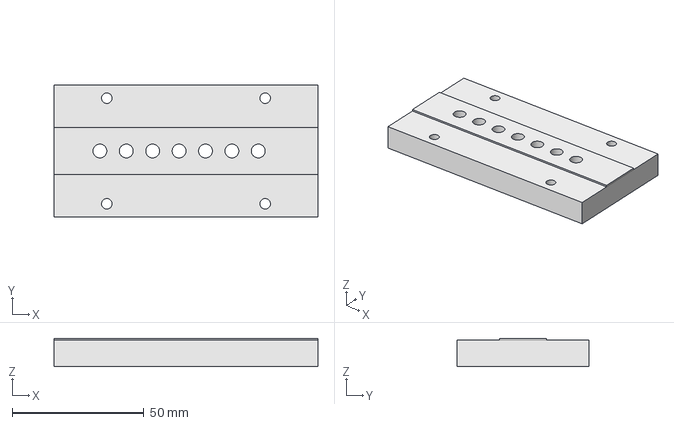
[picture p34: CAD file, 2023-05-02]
Misc/3D_Printed Components/TopBladeHolder(WiderBladePress)RevB.FCStd
100.0 x 50.0 x 10.7 mm

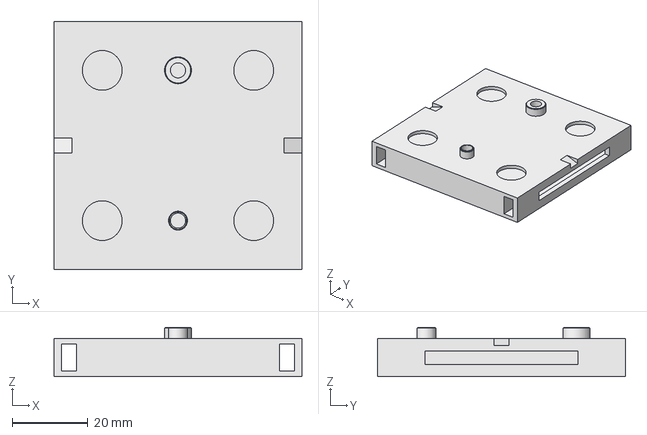
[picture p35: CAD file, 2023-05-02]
Misc/3D_Printed Components/BottomAdjBaseMountPlateNotchRevF.FCStd
65.5 x 65.5 x 13.0 mm

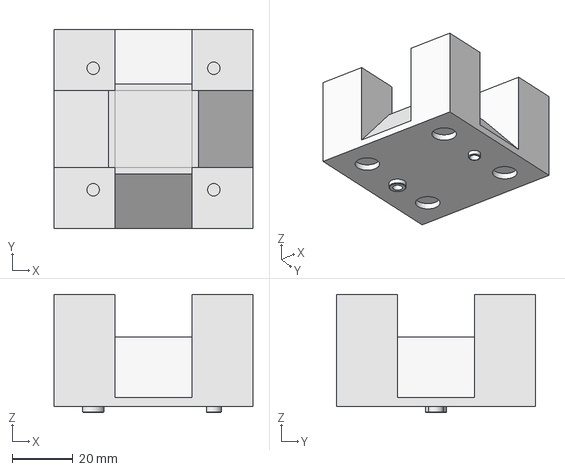
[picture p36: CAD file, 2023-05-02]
Misc/3D_Printed Components/Standoff.FCStd
65.5 x 65.5 x 39.0 mm

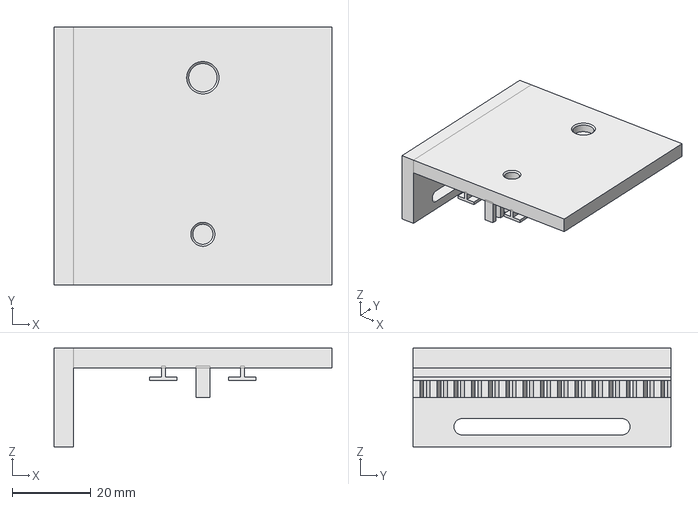
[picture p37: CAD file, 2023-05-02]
Misc/3D_Printed Components/Top10mmAdjRevD.FCStd
70.5 x 65.5 x 25.0 mm

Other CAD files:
Misc/3D_Printed Components/AdjBaseMountPlateRevD.FCStd

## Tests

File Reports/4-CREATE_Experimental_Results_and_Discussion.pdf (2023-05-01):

PP-2017 V2.1

ABRIDGED TITLE OF YOUR ACTIVITY | 1

# Automatic Paper Ream Opener Experimental Results and Discussion

Youssef Jalwaj Soubai, Mazin Chater, Abdullah Qurshrimp

Activity Report

✦

### 1 EXPERIMENTAL DESIGN

The experiment aimed to answer two questions:
Will a disabled employee be able to operate the apparatus after a 10 minute training brief and is the device safe and easy to use?
The previous experimental design aimed to gather data using the following metrics:
- Quality laceration success rate
- Ease of use rating from employees on a ten integer scale
- Safety rating from employees on a ten integer scale
Data was sought to be collected by having disabled employees perform the task of opening 50 reams of paper using the automated device after a 10 minute training session. The employees would be surveyed for feedback on the ease of use and safety of the apparatus. The number of paper reams put through the device would the independent variable, while the number of quality lacerations would the dependent variable.
The device aimed to control for safety by fully covering the razor blades utilized in the device, making them inaccessible to the user. The success of the experiment will be determined based on the number of paper reams
- Youssef Jalwaj-Soubai,
E-mail: yjalwaj-soubai@albany.edu,
- Mazin Chater,
E-mail: mchater3@albany.edu,
- Abdullah Qureshi,
E-mail: aqureshi@albany.edu, University at Albany.

that the disabled employee is able to open using the device. Any result greater than zero will be deemed as successful, since employees were previously not allowed to open reams due to physical dexterity and safety concerns. Ultimately, a disabled worker was given the task of opening two boxes of reams which amounted to 20 reams of paper. Due to time restrictions imposed on the workers, implementing a formal examination survey at the conclusion of their testing was deemed inappropriate. As such, verbal feedback during their testing was extremely valuable and essentially quantified the latter two metrics without the use of a survey.

### 2 RESULTS

The apparatus underwent rigorous testing with a mass amount of paper reams. The tests were conducted meticulously, pushing the machine to its limits,with the goal of showcasing exceptional reliability and efficiency. The table displayed in Figure 1 captures a snippet of the first thirteen tests performed and some brief comments concerning each individual test. Furthermore, the entirety of the testing log is visually depicted within Figure 2.

### 3 DISCUSSION

From the experimental data gathered, it is evident that implemented design is largely successful. To quantify a percentage, out of the 130 paper reams opened, only 7 had issues that prevented the ream from being opened

Activity Report

2 | ABRIDGED TITLE OF YOUR ACTIVITY

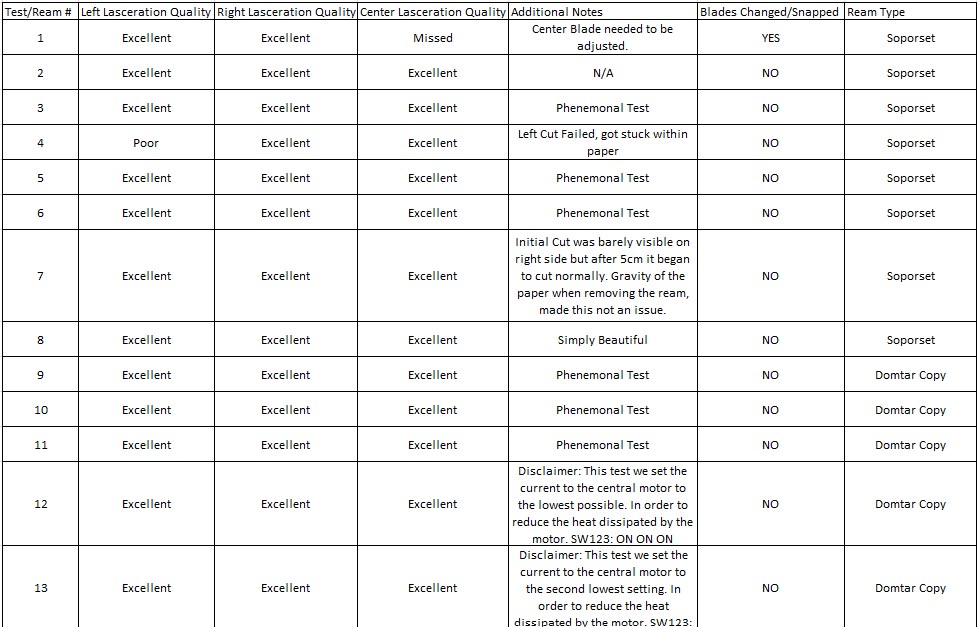
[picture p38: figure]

Figure 1. Data portion of the testing log. The earlier trials were the most informative and utilizing this knowledge the necessary adjustments were performed. Subsequently the latter tests have an overwhelming theme of success.

completely. This translates to a success rate of
roughly 95 percent which effectively satisfies the initial metric to achieve a quality laceration success rate. From verbal feedback gathered from employees at the facility, the latter metrics of safety and ease of use also received high marks.

### 3.1 Limitations & Future Work

Although the implemented design is largely successful, there are several aspects that can be improved if time constraints were not an issue. Observe:
- Smaller Scale: Although not a major concern considering the mailing facility has dedicated a cart for transportation of the device, having a smaller device could alleviate concerns about portability and overall system complexity.
- User-Friendly Features: Incorporating an LCD screen alongside LEDs could greatly improve ease of use and accessibility by making the design generally more pleasant to interact with.
- Removal of Outside Layer: The current implementation relies on three stepper motor controlled blades that cut adjacent sides of the ream but must be removed by the user. Future implementations could implement a more sophisticated model capable of removing this outside layer.

### 4 CONCLUSION

The automated paper ream was designed to address the issue of disabled employees who were unable to open paper reams by hand due to dexterity issues. To solve this problem, the machine was created such that the user only needed to place the packaged paper ream into

PP-2017 V2.1

SURNAME et al. | 3

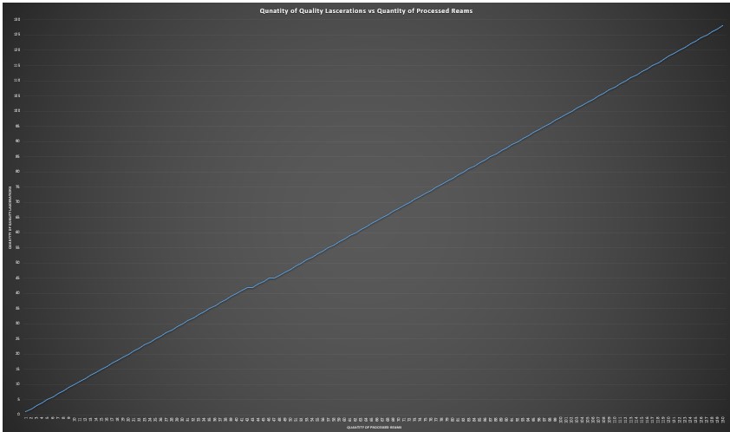
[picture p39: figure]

Figure 2. Visual depiction of the current data within the cumulative testing log.

the machine’s drawer and press the go button.
The machine contains three blades that apply
cuts on three sides of the paper ream, making it easy for the user to remove the package by flicking the paper ream and pulling it apart. Ensuring the safety of the machine’s users was a primary concern during its development. The machine’s blades and motors are completely enclosed, ensuring that there is no way for the user to put their hand inside the machine while it’s operating. Additionally, an emergency stop button was included to disable the machine from running and stop every stepper motor inside the machine the moment it is pressed. Once pressed, the user can restart the machine by pressing the go button, and the machine will restart in the same state as it was when the emergency stop button was pressed. Key accomplishments include providing opportunities for disabled employees being unable to open paper reams due to dexterity issues and ensuring the safety of the machine’s users through the inclusion of safety features such as fully enclosed blades and an emergency

stop button.

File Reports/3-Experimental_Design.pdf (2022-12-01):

PP-2017 V2.1

EXPERIMENTAL DESIGN | 1

# Automated Ream Opener (Experimental Design)

Youssef Jalwaj-Soubai, Mazin Chater, Abdullah Qureshi

Activity Report

✦

### 1 TESTING & EXPERIMENTAL DESIGN

### 1.1 Verification Testing

An integral part of constructing a valid design involves a thorough process of verification testing. This form of testing allows one to verify if a product meets the specifications and requirements previously written in the ”Logical Design”. First and foremost, a core requirement that must be investigated is the paper ream cutting ability of the apparatus. The system must be able to fashion precise lacerations on a paper ream with a consistent rate of success. Furthermore, another essential condition is safety and ease of use. This product will be utilized by employees with physical disabilities, as such designers have placed great emphasis on maintaining their well being and delivering a design that will be accident-proof. In order to test these qualities, the team will run tests at the mailing center with a sample size of fifty reams. Data will be collected from these experiments and conclusions will be drawn on the quality of cut, safety, and ease of use of the device. Specifically, one will ensure that the system is meeting core requirements by applying an iterative process of testing followed by design modifications. Repeating this loop will yield the most optimal solution.

- Youssef Jalwaj-Soubai,
E-mail: yjalwaj-soubai@albany.edu,
- Mazin Chater,
E-mail: mchater3@albany.edu,
- Abdullah Qureshi,
E-mail: aqureshi@albany.edu, University at Albany.

### 1.2 Validation Testing

In contrast, validation testing addresses how well the product has met the clients true needs and expectations. In order to do so, designers have developed an experiment that will test how effective the device is at solving the following problem statement. Which is to design and produce an automated tool that will allow a disabled person to easily open a ream of paper. Currently a disabled person cannot accomplish this task, due to a history of paper cuts inflicted upon the employees who attempted to do so. As such the following experiment will help designers confirm whether or not they have delivered a viable solution.

1.2.1 Experimental Questions
Specifically the following questions must be asked of this experiment:
- Question 1: Will a disabled employee be able to operate the apparatus after a 10 minute training brief?
- Question 2: Is the device safe and easy to use?

1.2.2 Hypothesis
If disabled employees are given a 10 minute training brief, then they will be able to operate the device easily in an effective and safe manner.
Furthermore, based off initial tests and determinations it is apparent that the correct answer to both experimental questions will be a resounding yes. The ultimate solution will consist of a singular button press. Therefore,

Activity Report

2 | EXPERIMENTAL DESIGN

there are zero other possible interactions with
the machine. This leaves the user with a convenient experience and emphasizes the notion of
ergonomic usage. Furthermore, the apparatus will be fully covered and as such the razor blades utilized within will be inaccessible to the user. Following this manner of thought accidents will be avoided entirely, because the only present risk has been fully accounted for.

1.2.3 Metrics
All projects should obtain hard data to measure the effectiveness of their system. The most important data in this context will be obtained directly from our end users. The following is a concise and direct list of desired metrics.
- Metric 1: Quality laceration success rate.
- Metric 2: Ease of use rating from employees on ten integer scale.
- Metric 3: Safety rating from employees on ten integer scale.

1.2.4 Data Collection
Adhering to the metrics provided above the data that will be collected concerns the success rate of obtaining a quality cut. This is defined by designers to be a laceration that fully dismembers the paper ream cover. Furthermore, the disabled employees will be surveyed for their feedback and as such the team will be able to garner data on the ease of use and safety of the apparatus. Of course this data will be collected via numerous trials. First designers will brief a disabled employee for ten minutes on how to use the device correctly. After doing so, the individual will be tasked with opening fifty reams of paper, while one of the team members stands by and observes their performance. The other members will be tasked with recording the data in live time. Especially making sure to note whether the now cut ream has passed the standard quality inspection. At the end of this trial, the employee will be given a questionnaire that will allow designers to gather information based on the users experience. This feedback will be an integral part of future design modifications. Furthermore, it is apparent from the data collection description that the independent variable will be the number of paper reams being put through the device, in other words our xaxis. Whereas, the dependent variable will be a running total of quality lacerations, the yaxis. Figure 1, displays a sample graph of what a possible test may yield. Continuing forward the experiment will control for bias by having a third party administer the questionnaire, refer to Figure 2. As such employees will not feel any pressure to answer in favor of the designers, since they will not be present. Also, the information will be collected anonymously in order to give individuals the chance to express their honest opinion. Lastly, after consulting with the professor the control was defined to be how many reams of paper a disabled employee could open without the device. The answer to this inquiry is zero. It is not safe for a disabled individual to do so manually due to the risk of paper cuts as noted previously. In that regard this experiment is special in nature because any result greater than zero can be deemed as successful. However, the designers will of course hold themselves to a standard of near perfection in the interest of assisting this noble cause. Upon obtaining a satisfactory volume of data, the team will meet once again and apply rationale engineering judgement to designing appropriate modifications based on user feedback. This cycle will continue to iterate until an optimal solution is uncovered.

PP-2017 V2.1

SURNAME et al. | 3

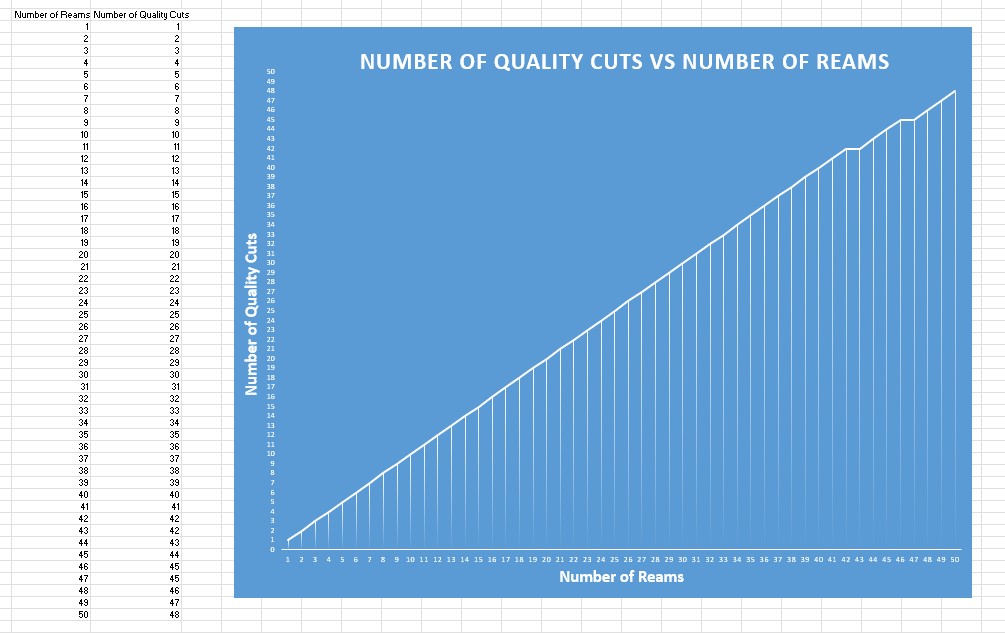
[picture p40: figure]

Figure 1. Example of possible data collection organized in line graph format. This illustrates a viable outcome from a live test.

Activity Report

4 | EXPERIMENTAL DESIGN

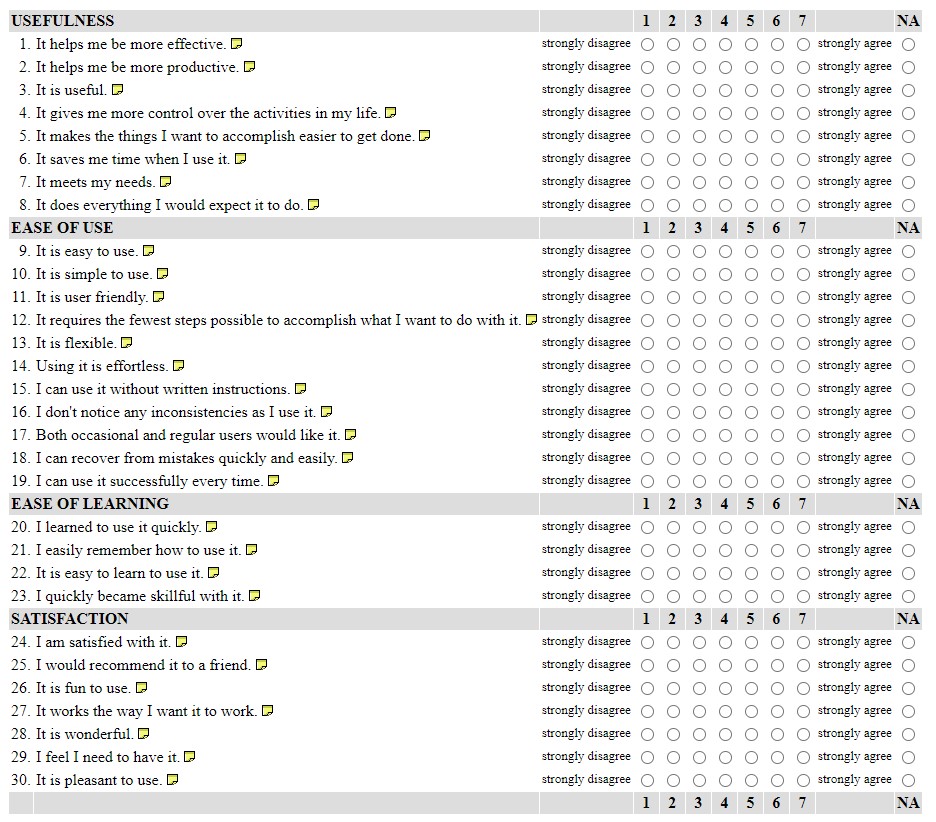
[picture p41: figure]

Figure 2. Example of possible questionnaire to be given to employees after conducting trials. Safety will be added as a section in the final copy of the survey.

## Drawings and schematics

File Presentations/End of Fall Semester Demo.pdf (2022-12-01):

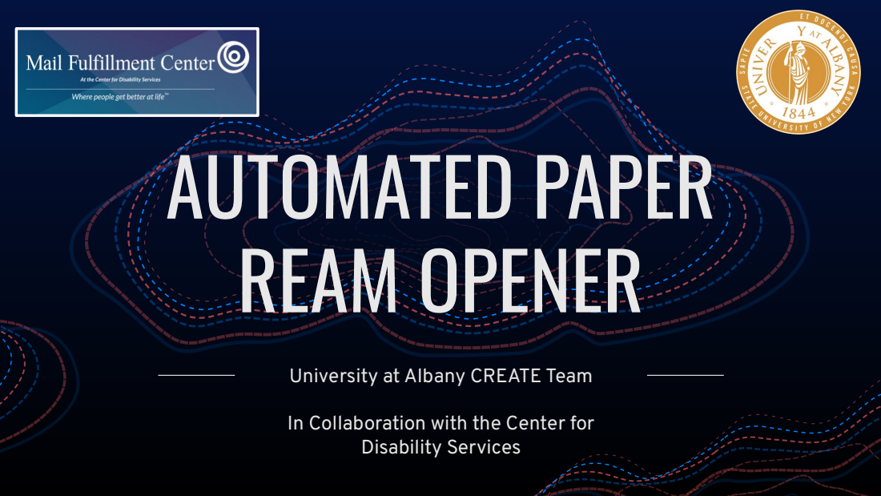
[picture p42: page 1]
Disability Services; AUTOMATED PAPER REAM OPENER

University at Albany CREATE Team

In Collaboration with the Center for

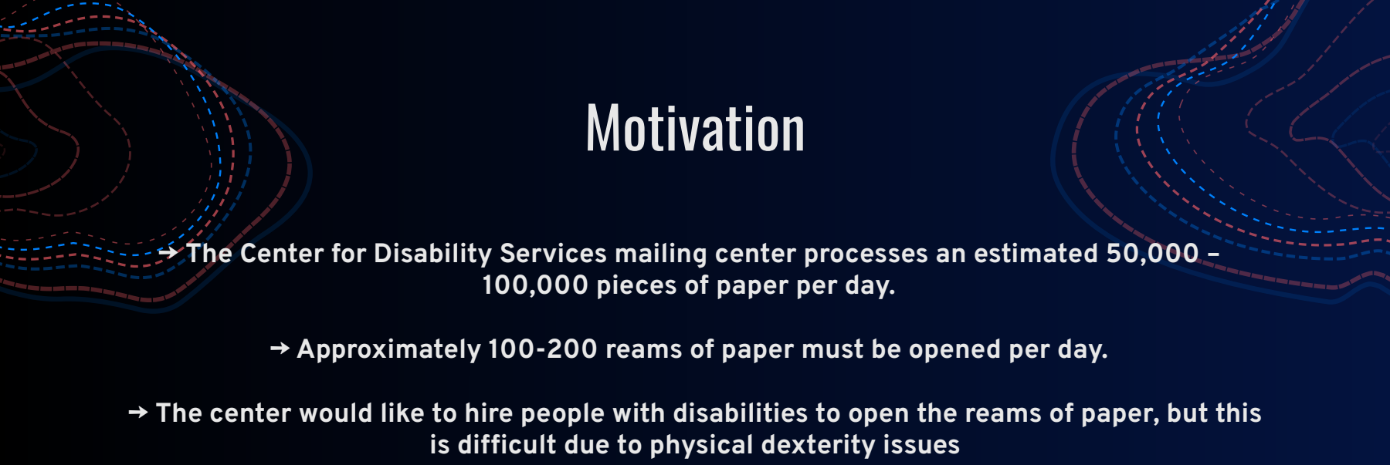
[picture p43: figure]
100,000 pieces of paper per day.; Motivation

→ The Center for Disability Services mailing center processes an estimated 50,000 –

→ Approximately 100-200 reams of paper must be opened per day.

→ The center would like to hire people with disabilities to open the reams of paper, but this is difficult due to physical dexterity issues

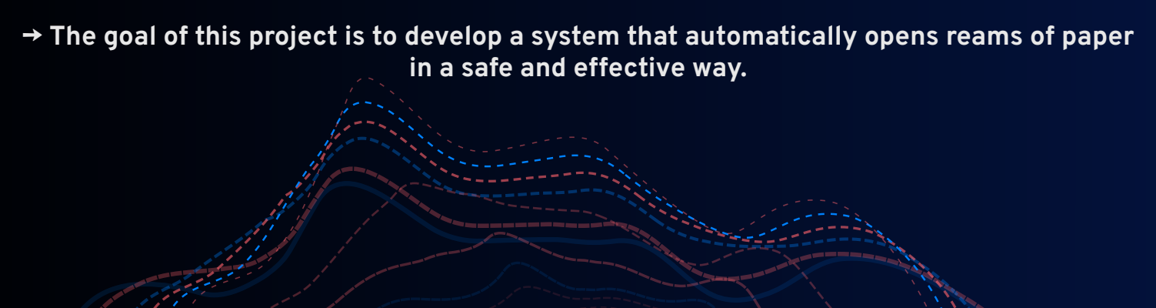
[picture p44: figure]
in a safe and effective way.

→ The goal of this project is to develop a system that automatically opens reams of paper

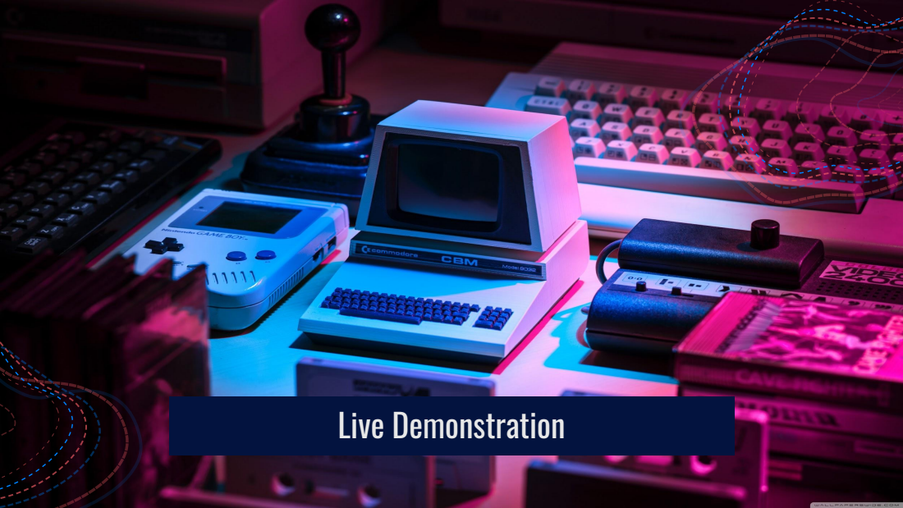
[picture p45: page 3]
Live Demonstration

# Logical Design

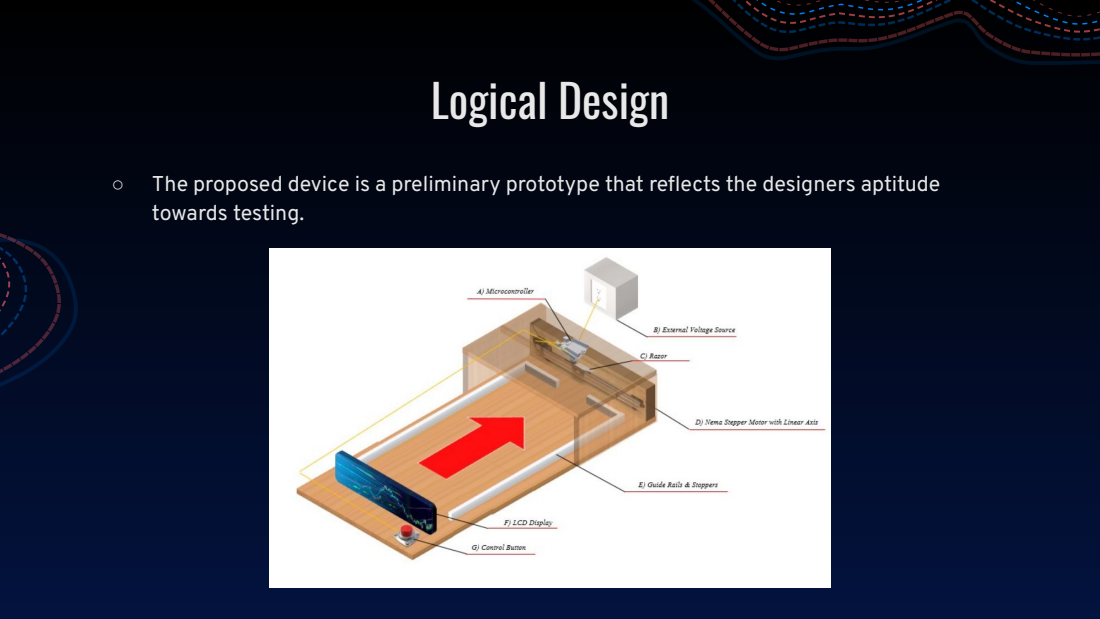
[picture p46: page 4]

○ The proposed device is a preliminary prototype that reflects the designers aptitude
towards testing.

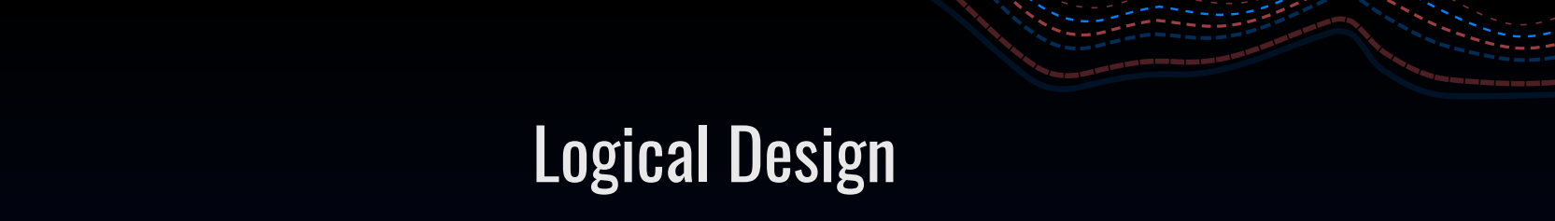
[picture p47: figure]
Logical Design

- The design is centered around a linear axis rail operated by a NEMA stepper motor.
- This combination makes the device capable of controlled uniform movement and as such when a razor blade is attached to the sliding linear cart it will ideally make clean lacerations to the paper ream cover.
- Along the base of the apparatus there are guiding protuberances that orient the ream in the most optimal setting. These ”stoppers” ensure that only the cover of the ream will be slit, thereby leaving the contents unperturbed.
- User interacts with the system via a button press that controls the operation of the linear rail.

# Physical Design

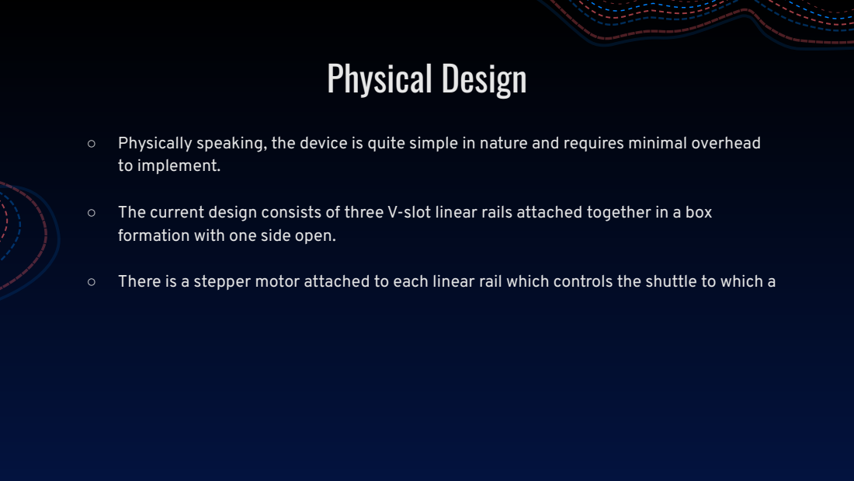
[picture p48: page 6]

○ Physically speaking, the device is quite simple in nature and requires minimal overhead
to implement.

○ The current design consists of three V-slot linear rails attached together in a box
formation with one side open.

○ There is a stepper motor attached to each linear rail which controls the shuttle to which a

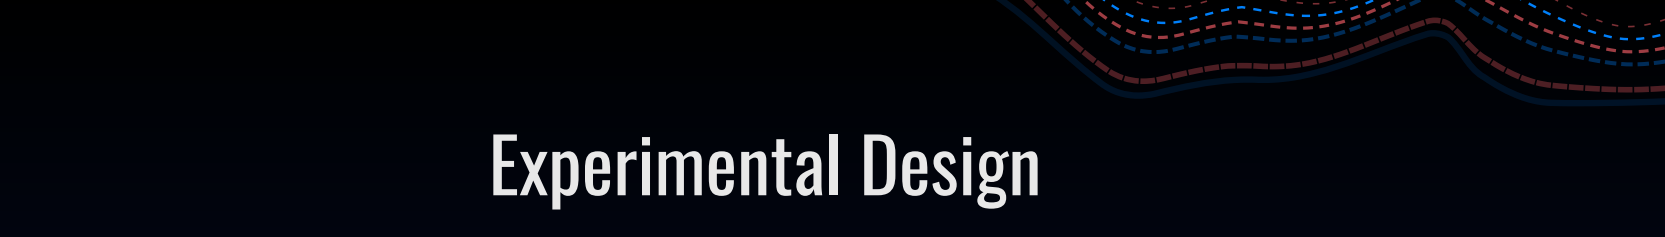
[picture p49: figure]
Experimental Design

- An integral part of constructing a valid design involves a thorough process of testing.
- A core requirement that must be investigated is the paper ream cutting ability of the apparatus.
- In order to test the final prototype, the system has to be tested with the paper ream multiple times.
- Since this product will be utilized by employees with physical disabilities safety is an essential testing condition.
- To ensure the safety of the employees the system will be completely enclosed.

# Upcoming Schedule

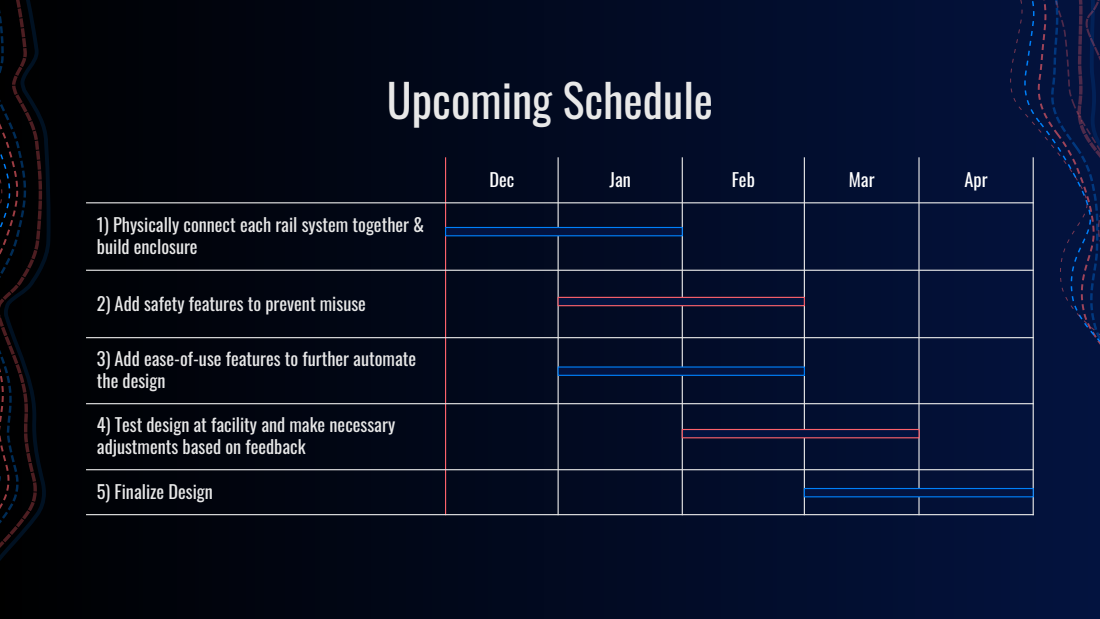
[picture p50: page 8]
Dec; Jan; Feb; Mar; Apr

1) Physically connect each rail system together &
build enclosure

2) Add safety features to prevent misuse

3) Add ease-of-use features to further automate
the design
4) Test design at facility and make necessary
adjustments based on feedback
5) Finalize Design

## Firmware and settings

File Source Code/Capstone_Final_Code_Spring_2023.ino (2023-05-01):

// CNC Shield Stepper  Control Demo


const int StepX = 4;
const int DirX = 7;
const int StepY = 3;
const int DirY = 6;
const int StepZ = 28;
const int DirZ = 29;
const int StepN = 22;
const int DirN = 23;
const int StartButtonPin = 25;
const int StopButtonPin = 24;
int StartButtonState = 0;
int StopButtonState = 0;


void setup() {

  Serial.begin(9600);
  pinMode(StartButtonPin, INPUT);
  pinMode(StopButtonPin, INPUT);
  pinMode(StepX, OUTPUT);
  pinMode(DirX, OUTPUT);
  pinMode(StepY, OUTPUT);
  pinMode(DirY, OUTPUT);
  pinMode(StepZ, OUTPUT);
  pinMode(DirZ, OUTPUT);
  pinMode(StepN, OUTPUT);
  pinMode(DirN, OUTPUT);

}

void resumeFun() {
  StartButtonState = digitalRead(StartButtonPin);
  if (StartButtonState == HIGH) {
    return;
  }
  else {
    Serial.println("Stop");
    resumeFun();
  }
}

int fullCycle() {
  Serial.println("FULL");

  delay(500);
  digitalWrite(DirX, HIGH); // set direction, HIGH for clockwise, LOW for anticlockwise
  digitalWrite(DirY, HIGH); // set direction, HIGH for clockwise, LOW for anticlockwise
  digitalWrite(DirN, LOW);

  for (int x = 0; x < 13300; x++) { // loop for 200 steps
    StopButtonState = digitalRead(StopButtonPin);
    if (StopButtonState == HIGH) {
      resumeFun();
    }
    if (x < 400) {
      digitalWrite(StepX, HIGH);
      digitalWrite(StepY, HIGH);
      digitalWrite(StepN, HIGH);
      delayMicroseconds(500);
      digitalWrite(StepX, LOW);
      digitalWrite(StepY, LOW);
      digitalWrite(StepN, LOW);
      delayMicroseconds(500);
    }
    else {
      digitalWrite(StepN, HIGH);
      delayMicroseconds(500);
      digitalWrite(StepN, LOW);
      delayMicroseconds(500);
    }
  }
  //delay(1000);

  /* for (int x = 0; x < 300; x++) { // loop for 200 steps
     StopButtonState = digitalRead(StopButtonPin);
     if (StopButtonState == HIGH) {
       resumeFun();
     }
     digitalWrite(StepX, HIGH);
     digitalWrite(StepY, HIGH);
     delayMicroseconds(1000);
     digitalWrite(StepX, LOW);
     digitalWrite(StepY, LOW);
     delayMicroseconds(1000);
    }*/
  //delay(1000); // delay for 1 second


  digitalWrite(DirZ, HIGH);

  for (int x = 0; x < 1250; x++) { // loop for 200 steps
    StopButtonState = digitalRead(StopButtonPin);
    if (StopButtonState == HIGH) {
      Serial.println("S");
      resumeFun();
    }
    digitalWrite(StepZ, HIGH);
    delayMicroseconds(1000);
    digitalWrite(StepZ, LOW);
    delayMicroseconds(1000);
  }
  //delay(1000); // delay for 1 second

  /*for (int x = 0; x < 300; x++) { // loop for 200 steps
    StopButtonState = digitalRead(StopButtonPin);
    if (StopButtonState == HIGH) {
      resumeFun();
    }
    digitalWrite(StepX, HIGH);
    digitalWrite(StepY, HIGH);
    delayMicroseconds(1000);
    digitalWrite(StepX, LOW);
    digitalWrite(StepY, LOW);
    delayMicroseconds(1000);
    }*/
  //delay(1000); // delay for 1 second

  delay(500);
  digitalWrite(DirX, LOW); // set direction, HIGH for clockwise, LOW for anticlockwise
  digitalWrite(DirY, LOW); // set direction, HIGH for clockwise, LOW for anticlockwise
  digitalWrite(DirN, HIGH);

  for (int x = 0; x < 13500; x++) { // loop for 200 steps
    StopButtonState = digitalRead(StopButtonPin);
    if (StopButtonState == HIGH) {
      resumeFun();
    }
      digitalWrite(StepN, HIGH);
      delayMicroseconds(500);
      digitalWrite(StepN, LOW);
      delayMicroseconds(500);
  }
  //delay(1000); // delay for 1 second

  for (int x = 0; x < 400; x++) { // loop for 200 steps
    StopButtonState = digitalRead(StopButtonPin);
    if (StopButtonState == HIGH) {
      resumeFun();
    }
      digitalWrite(StepX, HIGH);
      digitalWrite(StepY, HIGH);
      delayMicroseconds(1000);
      digitalWrite(StepX, LOW);
      digitalWrite(StepY, LOW);
      delayMicroseconds(1000);
  }

  digitalWrite(DirZ, LOW);

  for (int x = 0; x < 1250; x++) { // loop for 200 steps
    StopButtonState = digitalRead(StopButtonPin);
    if (StopButtonState == HIGH) {
      resumeFun();
    }
    digitalWrite(StepZ, HIGH);
    delayMicroseconds(1000);
    digitalWrite(StepZ, LOW);
    delayMicroseconds(1000);
  }
  //delay(1000); // delay for 1 second

  return 1;
}

void loop() {

  StartButtonState = digitalRead(StartButtonPin);

  //Towards Motor

  if (Serial.available() > 0) {

    char inByte = Serial.read();

    if (inByte == 'u') {

      delay(300);
      digitalWrite(DirX, HIGH); // set direction, HIGH for clockwise, LOW for anticlockwise
      digitalWrite(DirY, LOW); // set direction, HIGH for clockwise, LOW for anticlockwise
      digitalWrite(DirZ, HIGH);
      Serial.println("UP");
      for (int x = 0; x < 1000; x++) {
        char inByte = Serial.read();
        if (inByte == 's') {
          Serial.println("Break");
          break;
        }
        digitalWrite(StepX, HIGH);
        digitalWrite(StepY, HIGH);
        delayMicroseconds(500);
        digitalWrite(StepX, LOW);
        digitalWrite(StepY, LOW);
        delayMicroseconds(500);
      }

      delay(1000);

      for (int x = 0; x < 800; x++) {
        char inByte = Serial.read();
        if (inByte == 's') {
          Serial.println("Break");
          break;
        }
        digitalWrite(StepZ, HIGH);
        delayMicroseconds(500);
        digitalWrite(StepZ, LOW);
        delayMicroseconds(500);
      }

      delay(1000);

    }



    // Away

    else if (inByte == 'd') {

      delay(300);
      digitalWrite(DirX, LOW); // set direction, HIGH for away from motor, LOW for towards motor
      digitalWrite(DirY, HIGH); // set direction, HIGH for away from motor, LOW for towards motor
      Serial.println("DOWN");
      for (int x = 0; x < 1000; x++) {
        char inByte = Serial.read();
        if (inByte == 's') {
          Serial.println("Break");
          break;
        }
        digitalWrite(StepX, HIGH);
        digitalWrite(StepY, HIGH);
        delayMicroseconds(500);
        digitalWrite(StepX, LOW);
        digitalWrite(StepY, LOW);
        delayMicroseconds(500);
      }
      delay(1000);

      digitalWrite(DirZ, LOW);
      for (int x = 0; x < 800; x++) {
        char inByte = Serial.read();
        if (inByte == 's') {
          Serial.println("Break");
          break;
        }
        digitalWrite(StepZ, HIGH);
        delayMicroseconds(500);
        digitalWrite(StepZ, LOW);
        delayMicroseconds(500);
      }

      delay(1000);


    }
    else if (inByte == 'f') {

      fullCycle();
    }
    else if (inByte == 'q') {

      digitalWrite(DirN, HIGH);
      for (int x = 0; x < 5000; x++) { // loop for 200 steps
        digitalWrite(StepN, HIGH);
        delayMicroseconds(500);
        digitalWrite(StepN, LOW);
        delayMicroseconds(500);
      }
      delay(1000); // delay for 1 second

    }
    else if (inByte == 'w') {

      digitalWrite(DirN, LOW);
      for (int x = 0; x < 5000; x++) { // loop for 200 steps
        digitalWrite(StepN, HIGH);
        delayMicroseconds(500);
        digitalWrite(StepN, LOW);
        delayMicroseconds(500);
      }
      delay(1000); // delay for 1 second
    }

  }

  if (StartButtonState == HIGH) {
    fullCycle();
  }
}
